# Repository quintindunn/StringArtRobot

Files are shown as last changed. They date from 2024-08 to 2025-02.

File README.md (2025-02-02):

# StringArtRobot

### **\*Important\***
### This project is NOT completed, and is going through more revisions. I would not recommend building it, unless you've gone over everything and too agree it will work, even then that's do it at your own risk!

## About
This is a project to automatically make string art from an input image. I got the idea for this project from [this](https://www.youtube.com/watch?v=WGccIFf6MF8&ab_channel=VirtuallyPassed) YouTube video by [Virtually Passed](https://www.youtube.com/@virtually_passed).
The logic for generating the sequences is based off [this gist](https://gist.github.com/kaspermeerts/781f0137b361b51224dcab722ae387b4#file-stringart-py) by [kaspermeerts](https://github.com/kaspermeerts), implemented in my [threadArt python library](https://github.com/quintindunn/threadArt).

## Video
*Not created yet*

## Design
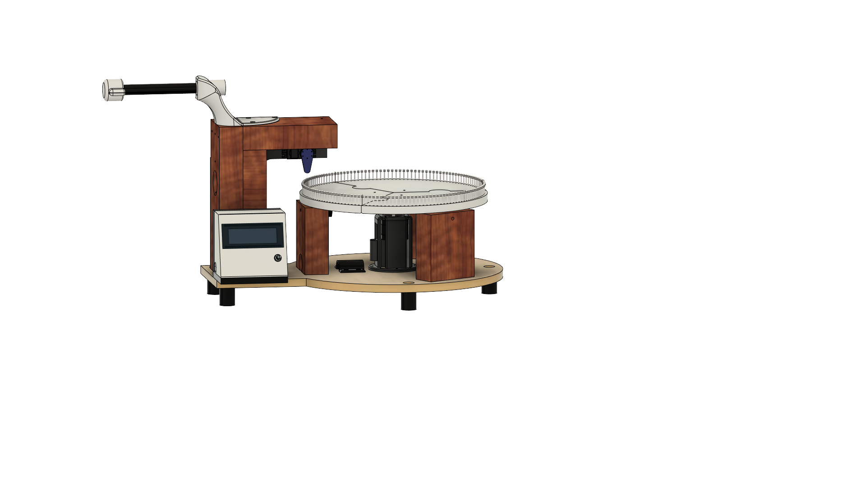
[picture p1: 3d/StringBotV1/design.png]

This project was modeled in Fusion360, with schematics made with EasyEDA (WIP)

## What you need to assemble this
**NOT A FULL LIST**
- 1x 2'x2' Sheet of 1/2" plywood
- 3x 4.25” long 2x4
- 2x 6” long 2x4
- 1x 8” 2x4
- 1x 9.5” 2x4
- Bunch of screws (Types not decided yet)
- 40mm x 0.45mm Sewing Needle
- Ender 3 Pro X-Axis stepper motor
- 3D printer & filament
- MG996R with circular horn
- Arduino Uno
- TMC2209 Stepper motor driver
- 12v 5a Power supply
- [Simthread Embroidery Thread](https://www.amazon.com/gp/product/B0BFWVR72D/ref=ppx_yo_dt_b_asin_title_o03_s00?ie=UTF8&th=1)

## Printing Instructions
Download the STL files from [/3d/StringBotV1](https://github.com/quintindunn/StringArtRobot/tree/main/3d/StringBotV1) <br>
Printed on an Ender 3 S1 Pro running octoprint.
### My general config, though check for any changes for the given part:
- Filament: Generic PLA
- Hotend Temperature: 200c
- Bed Temperature: 60c
- Infill: 20%
- Slicer: PrusaSlicer 2.5.2
- Supports: Off

### Part by part breakdown (INCOMPLETE)
| Name | Quantity | Material | Infill | Supports | Orientation |
|---|---|---|---|---|---|
| N/A  | N/A | N/A | N/A | N/A | N/A |

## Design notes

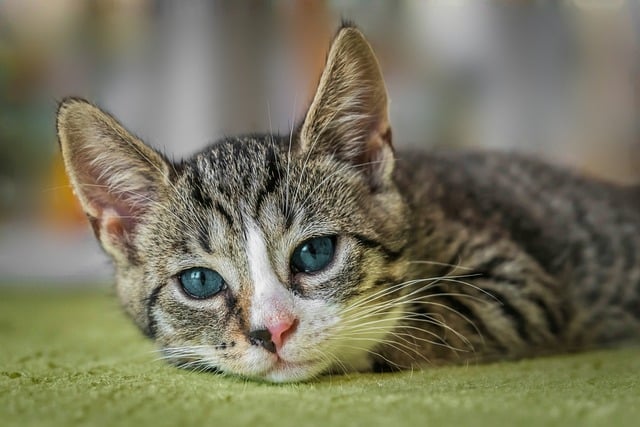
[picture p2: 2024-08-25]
target/cat.jpg

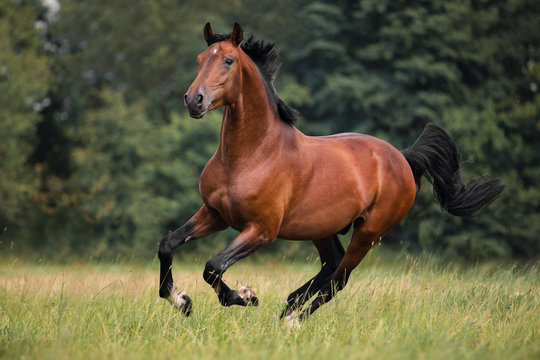
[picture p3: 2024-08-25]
target/horse.jpg

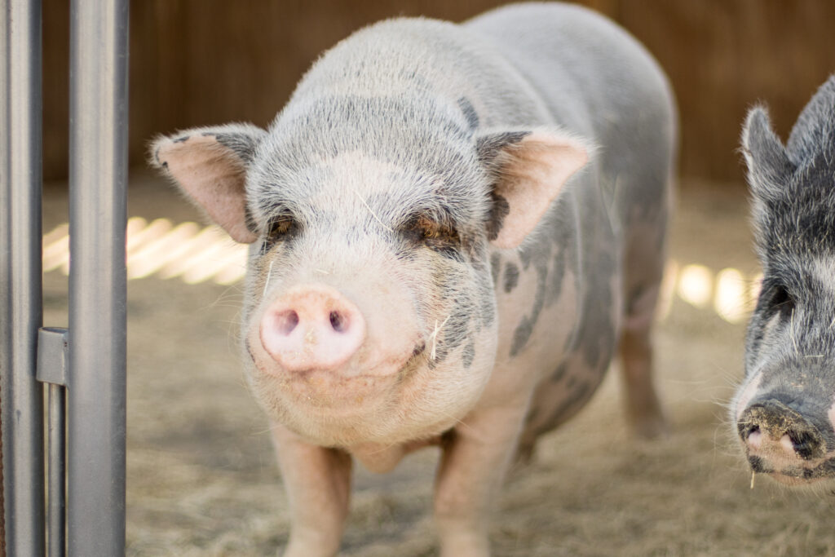
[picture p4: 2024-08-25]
target/pig.jpg

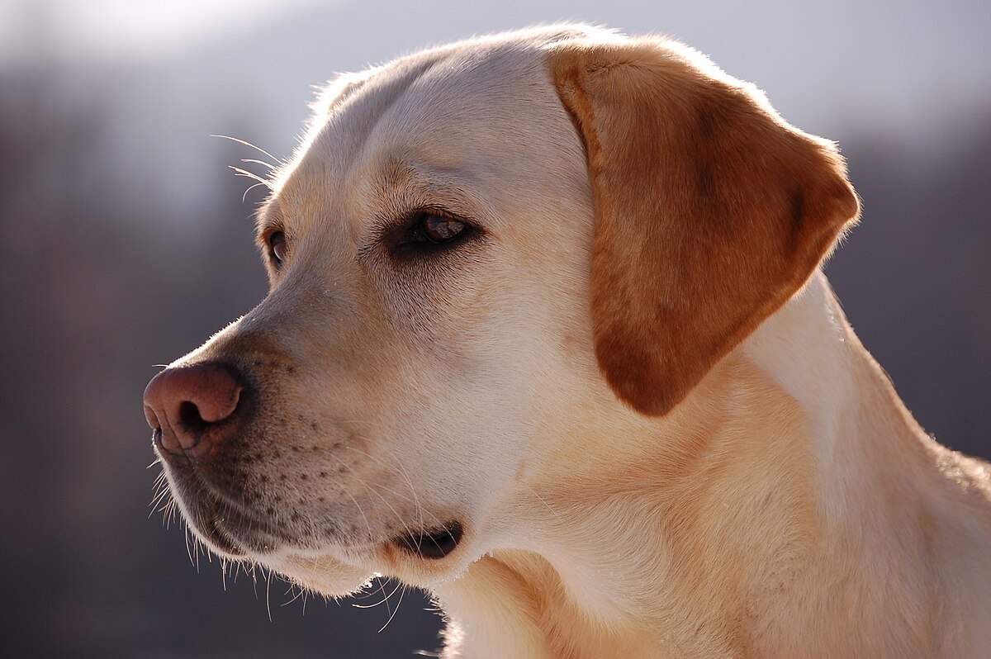
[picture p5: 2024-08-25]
target/dog.jpg

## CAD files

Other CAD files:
3d/StringBotV1/v1.f3d

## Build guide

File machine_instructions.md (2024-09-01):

# DOCUMENTATION:
## Rotate Table:
### Parameters:
    * degrees - How many degrees to rotate
    * direction - Which direction to rotate (Direction.CW | Direction.CCW)
    * speed - 0-255 How quickly to rotate the table
### Instruction:
    * ROT d<direction> a<degrees> s<speed>

## Place Nail:
### Parameters:
    * ps - 0-255 How quickly to place the nail
    * rs - 0-255 How quickly to retract the tool
### Instruction:
    * PN p<ps> r<rs>

## Move Tool:
### Parameters:
    * tool_id - The numerical ID of the tool
    * delta_x - The change in the `x` value
    * delta_y - The change in the `y` value
    * speed - 0-255 How quickly to move the tool
### Instruction:
    * MT i<tool_id> x<delta_x> y<delta_y> s<speed>

## Beep:
### Parameters:
    * duration_ms - how long to beep for (ms)
    * repeat - How many times should it repeat for
    * off_time_ms - How long between beeps (ms)
### Instruction:
    * BP d<duration_ms> r<repeat> o<off_time_ms>

## Sleep:
### Parameters:
    * duration_ms - How long to sleep for (ms)
### Instruction:
    * SP d<duration_ms>

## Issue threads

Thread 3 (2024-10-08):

Servo value must be between -1 and 1, or None

quintindunn, 2024-10-08:
```
Command: Exception in thread Thread-3 (execute_file):
Traceback (most recent call last):
  File "/usr/lib/python3.12/threading.py", line 1073, in _bootstrap_inner
    self.run()
  File "/usr/lib/python3.12/threading.py", line 1010, in run
    self._target(*self._args, **self._kwargs)
  File "/home/quintindunn/stringartrobot/robot/robot/string_bot.py", line 53, in execute_file
    instruction.execute()
  File "/home/quintindunn/stringartrobot/robot/robot/instructions.py", line 126, in execute
    rotate_arm_to(degrees=self.degrees)
  File "/home/quintindunn/stringartrobot/robot/robot/hardware_api/rotate_servo.py", line 33, in rotate_arm_to
    servo.value = degrees
    ^^^^^^^^^^^
  File "/home/quintindunn/.local/lib/python3.12/site-packages/gpiozero/devices.py", line 454, in __setattr__
    return super().__setattr__(name, value)
           ^^^^^^^^^^^^^^^^^^^^^^^^^^^^^^^^
  File "/home/quintindunn/.local/lib/python3.12/site-packages/gpiozero/devices.py", line 130, in __setattr__
    return super().__setattr__(name, value)
           ^^^^^^^^^^^^^^^^^^^^^^^^^^^^^^^^
  File "/home/quintindunn/.local/lib/python3.12/site-packages/gpiozero/output_devices.py", line 1622, in value
    raise OutputDeviceBadValue(
gpiozero.exc.OutputDeviceBadValue: Servo value must be between -1 and 1, or None
```

Working servo code, needs to adapt program to use this method:
```py
def set_servo_angle(angle):
    # Clamp the angle between -90 and 90 degrees
    angle = max(-90, min(90, angle))
    # Convert angle (-90 to 90) to value (-1 to 1)
    value = angle / 90
    servo.value = value
```

Closed 2024-10-09.

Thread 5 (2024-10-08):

Generator/Slicer not working

quintindunn, 2024-10-08:
Generator/Slicer needs to move the arm to the forwards position prior to travel to next pin, after final loop around it should stay in the forward position to keep tension on the thread.

quintindunn, 2024-10-09:
I think I've worked out a sequence to loop around a given pin:

Variables:
`fw -> forward angle (arm)`
`bw -> backward angle (arm)`
`d1 -> Clockwise (CW)`
`d2 -> Counter-Clockwise (CCW)`
`spacing = 360/pin_count`

Sequence:
1.) Rotate to the pin
2.) Rotate `d1` `spacing/2`deg
3.) Arm from `fw`deg -> `bw`deg
4.) Rotate `d2` `spacing`deg
5.) Arm from `bw`deg -> `fw`deg
6.) Rotate `d1` `spacing`deg
7.) Arm from `fw`deg -> `bw`deg
8.) Rotate `d2` `spacing`deg
9.) Arm from `bw`deg to `fw`deg

Not able to test this right now as I'm printing a new design for the stepper mount, but will implement this on a generator branch.

quintindunn, 2024-10-17:
Complete rework of how the motor interprets rotational commands, moving from relative positioning to absolute position relative to the zero'd position of the motor. (#6, #7)

This seems to be working as I anticipated now even without real world testing through simulation from my [StringArtRobotSimulator](https://github.com/quintindunn/StringArtRobotSimulator) project. Hopefully any further tuning can be conducted strictly through the parameters I added to the generator, likely specifically the Table sleep time (`tbsp`), which is the time in milliseconds between the motor finishing a movement and the next command to be executed in the sequence.

Closed 2024-10-17.

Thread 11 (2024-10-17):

Stepper motor not driving

quintindunn, 2024-10-17:
I'm not quite sure the problem, it may be due to current/voltage, or the wiring of the `stepper -> TMC2209`. The wiring should be the same as [this schematic](https://github.com/quintindunn/StringArtRobot/blob/design/design/StringBotV1/wiring/Schematic_StringArtBot_2024-10-05.pdf). When driving it it runs at very low power even with the current pot set to the highest value, then occasionally if I disable it (move `en` pin from LOW to HIGH) then re-enable it, the current will go to expected levels. The stepper occasionally works, but more then not will have a very jerky motion, unable to pick a direction, and when it finally starts driving has very little torque. I believe the stepper is wired correctly, though at this point I'm very confused. I wonder if the driver is maybe drawing too much current for the RPI Z 2W to handle, causing more of an oscillation than a step, though I don't think that is the case.

When I get home later I plan on putting a 5v, 5a power supply in parallel with the RPI 5v line.

If anyone comes across this and has any input as to why it's doing that it would be greatly appreciated.

quintindunn, 2024-10-17:
While reading the datasheet I saw something about the DIAG pin signaling when the driver would need to be rest as I described above, I see it has tools for diagnostics built in, so I'll probably try using those when I get home.

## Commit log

2024-08-27 Bumped threadArt to 1.0.4
2024-08-28 Added v1 model
    [v1.f3d]
2024-08-30 Bumped threadArt
2024-09-01 Updated to threadArt 1.2.0 for a more accurate algorithm
2024-09-04 Added placeholder motor controls
2024-10-05 Added time to travel for arm
2024-10-09 Clamped angle between -90, 90, converted into a value -1 -> 1. Fixing issue #3
2024-10-14 Fixed servo angle clamping to also run on the first usage of rotate_arm_to(), fully fixing #3
2024-10-14 Updated GPIO pins to match schematic
2024-10-15 Revert "Switch to absolute angle system"
